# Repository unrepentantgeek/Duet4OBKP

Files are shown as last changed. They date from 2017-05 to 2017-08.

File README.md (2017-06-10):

# Duet4OBKP
Duet Wifi upgrades for the OpenBeam Kossel Pro

## Introduction
This is a set of 3D printed parts and instructions to upgrade the OpenBeam Kossel Pro to use the Duet Wifi (or Duet Ethernet) electronics.  The parts may also fit other printers that share similar geometry.

## The basics
The basic upgrade requires only the Duet motherboard and a 30mm fan, plus two printed parts for mounting and protecting the electronics.
  * Duet Wifi [US](https://www.filastruder.com/collections/electronics/products/duet-wifi) [EU](https://www.duet3d.com/DuetWifi)
  * 30mm 5V fan
  * [Panel mount USB cable](https://www.adafruit.com/product/937) (optional)

## Touchscreen
The PanelDue controller and touchscreen give you front panel monitoring and access to most of the functions of the printer.  It is available in 3 screen sizes, and printed enclosures are available for each.  Note that the 7" display enclosure is very large and may require removal of two bed clamps to be printable on the Kossel Pro.
  * PanelDue [US](https://www.filastruder.com/collections/electronics/products/paneldue) [EU](https://www.duet3d.com/DuetAddons/PanelDue)

## Hotend
The E3D hotend is one of the best, and the E3D lite is an amazing value.  With a couple of printed parts the end effector can be upgraded to fit either one.  Just make sure that you get the 24v heater to match the Kossel Pro's power supply.  You will also need to obtain another 5v 30mm fan (4.3CFM) as the Kossel Pro end effector PCB cannot handle 24v.
  * E3D Lite V6 (24v bowden) [US](https://www.filastruder.com/products/lite6?variant=1283850628) [EU](http://e3d-online.com/Lite6-1.75mm-Bowden-24v)
  * E3D V6 (24v bowden) [US](https://www.filastruder.com/products/all-metal-e3d-v6-hotend?variant=1236046392) [EU](http://e3d-online.com/E3D-v6/Full-Kit/175-universal-bowden-full-kit)
  * 30mm 5v fan (4.3CFM)

## Streaming webcam
You can mount a Raspberry Pi Zero W in the offical case with a camera and cheap wide angle lens to get streaming video in the web interface of your printer.
  * [Raspberry Pi Zero W Camera pack](https://www.adafruit.com/product/3414)
  * [Wide angle cell phone lens](https://www.amazon.com/Aduro-Universal-Magnetic-Detachable-Smartphones/dp/B01N2REG4L)

## PEI/Ultem print surface
This is an inexpensive and highly recommended upgrade for improved bed adhesion.
  * [Gizmo Dorks PEI Sheet](https://www.amazon.com/Gizmo-Dorks-Printing-Surface-Adhesive/dp/B01KGDTNQ2)

## The process
* [Preparation](Preparation.md)
* [Assembly](Assembly.md)
* [Configuration](Configuration.md)
* [Calibration](Calibration.md)

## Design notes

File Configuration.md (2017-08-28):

# Configuration

## Offline

Power down your printer and remove the micro-SD card from the Duet and connect it to your computer.  Copy the files in [sys](sys) to /sys on the SD card, overwriting files of the same name.

## Online

Follow the [directions to get your Duet online](https://duet3d.com/wiki/Getting_connected_to_the_Duet_WiFi) and use the web interface (settings tab) to update the contents of the corresponding files in [sys](sys).

### M500 and M501

* Note: Your Duet must be running ReprapFirmware 1.17 or higher for M500/M501 support.  [How to check your firmware version](https://duet3d.com/wiki/Checking_the_firmware_versions_and_updating_the_firmware)

The `M500` command will write out your system calibration to `/sys/config-overrides.g`.  Running the `M501` command will load that file and set those parameters.  To simplify recalibration we have added the `M501` command to the end of the `config.g` file.  Any time you want to save your current settings run `M500` and they will be stored for loading at the next reset.  The settings stored by `M500` are:

  * Delta parameters (`M666` and `M665`)
  * Heater paramters (`M307`)
  * Z probe parameters (`G31`)

The rest of the instructions assume that you will use `M500` to store these settings.

### Updating your configs

You can update config.g directly, or write overrides into local.g which is executed at the end of config.g, but before the calibration settings are loaded with `M501`.  If you use local.g then you can easily update config.g from this repository while maintaining your own changes.

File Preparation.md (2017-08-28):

## Tools
The tools that came with your Kossel Pro will get you most of the way.  You'll also need to buy or borrow some specialized tools for terminating the wires for the new connections:

- [Ferrule Crimper with Ferrules](https://www.amazon.com/gp/product/B01K160CC8/)
- [Ratcheting crimp pliers](https://www.adafruit.com/product/1213)
- [Wire stripper](https://www.amazon.com/IRWIN-VISE-GRIP-Self-Adjusting-Stripper-2078300)

A 2.5mm drill and an M3 tap are also recommended for forming threads in the plastic parts.

## Print the parts

## Strip the printer
Unplug power first and let it sit a few minutes at least.

To ease disassebly, you can cut the power input and heated bed output wires right at the Brainwave Pro motherboard.  We will
re-use these wires with new ends on them during assembly.

Disassembly:
  Remove end effector
  Remove delta arms
  Remove print glass & heated bed
  Remove bed clamp assemblies
  Remove power inlet/switch bulkhead and wires to the PSU
  Disconnect all wires and remove Brainwave Pro mainboard
  Remove extruder cold end assembly

If you didn't add the extra m3 nuts to the lower frame rails as recommended in the assembly guide, then you'll need to go back now and add them.  This is an exercise left to the reader, but turning the printer upside down and removing one rail at a time can be helpful.

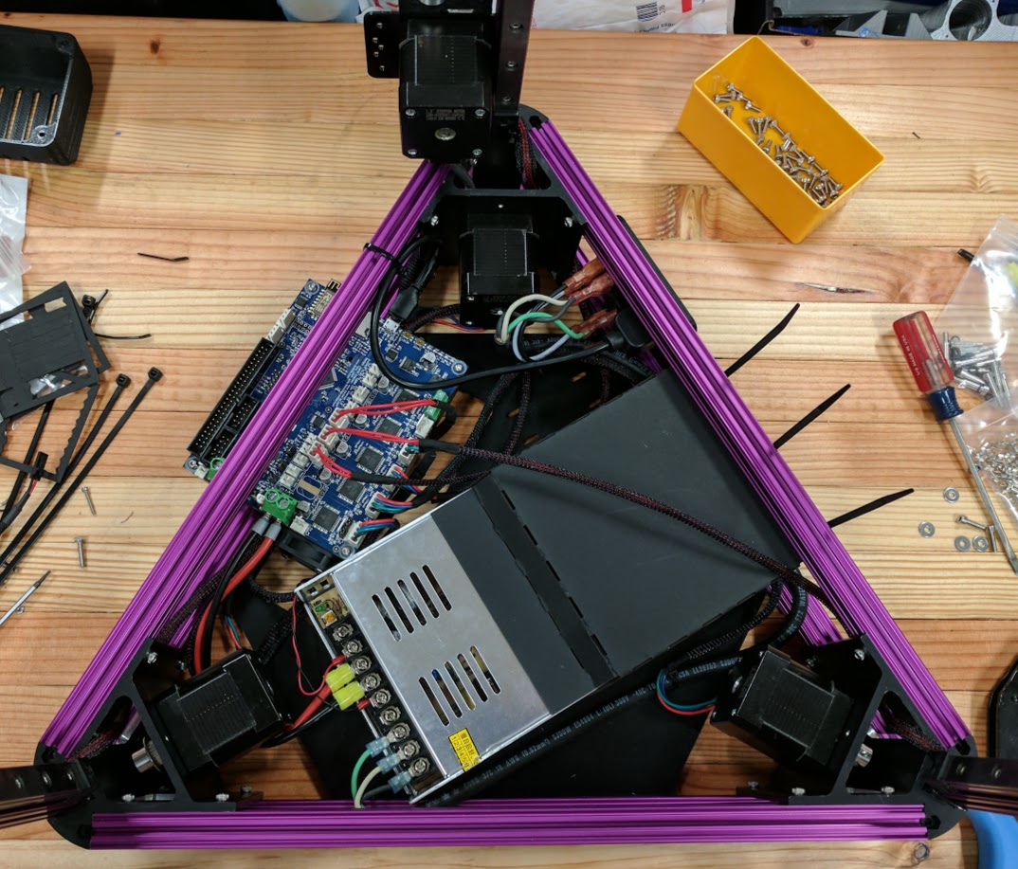
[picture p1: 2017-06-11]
img/lower_frame.jpg

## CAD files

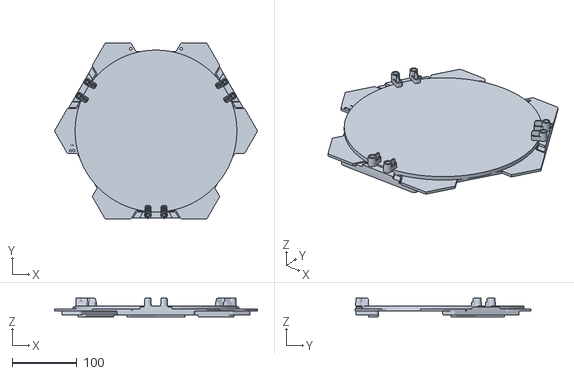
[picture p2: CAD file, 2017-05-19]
slicer_configs/openbeamkosselpro.stl
313.8 x 272.0 x 29.0

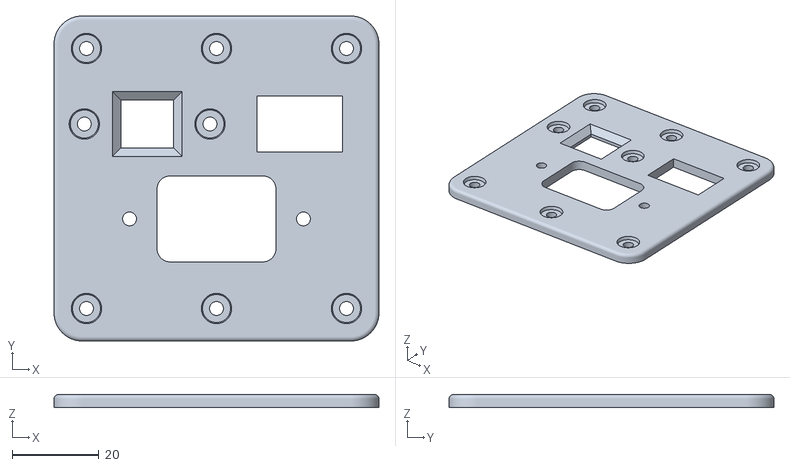
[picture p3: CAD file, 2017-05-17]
stl/Combination Bulkhead.stl
75.0 x 75.0 x 3.00

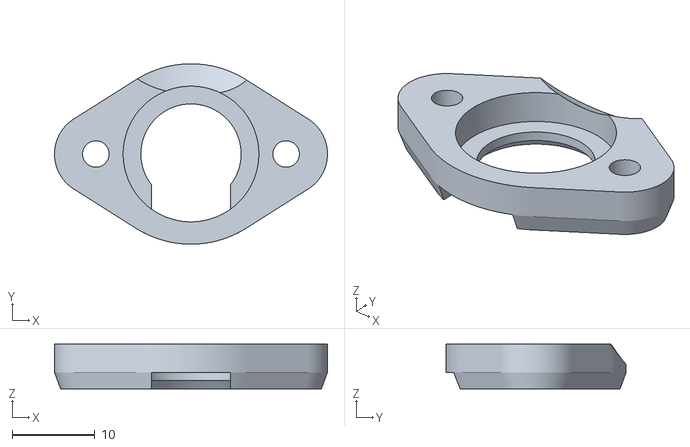
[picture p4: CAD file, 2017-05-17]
stl/Hot end clamp - Upper.stl
33.0 x 21.8 x 5.40

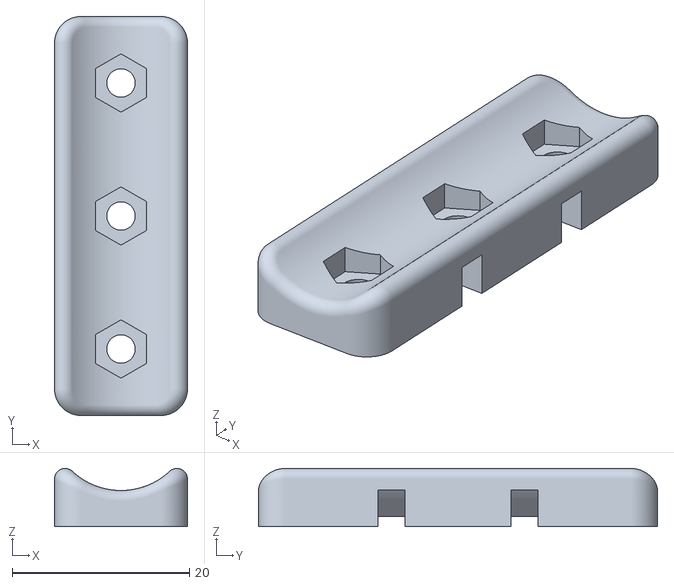
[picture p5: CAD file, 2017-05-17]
stl/Wire Mount.stl
15.0 x 45.0 x 6.56

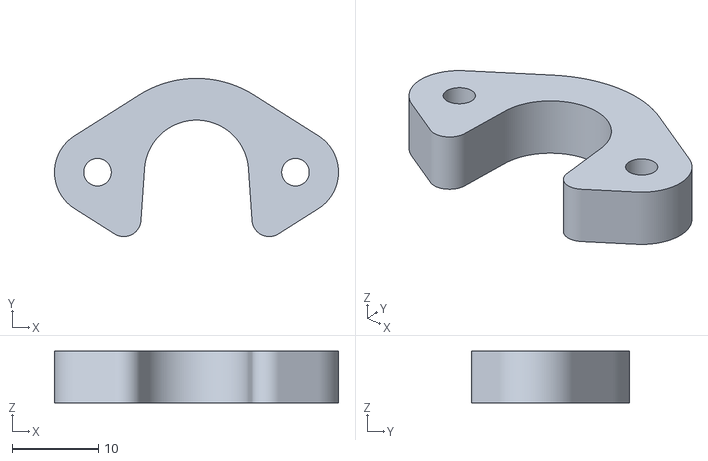
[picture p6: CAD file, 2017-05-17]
stl/Hot end clamp - Lower.stl
33.0 x 18.4 x 6.00

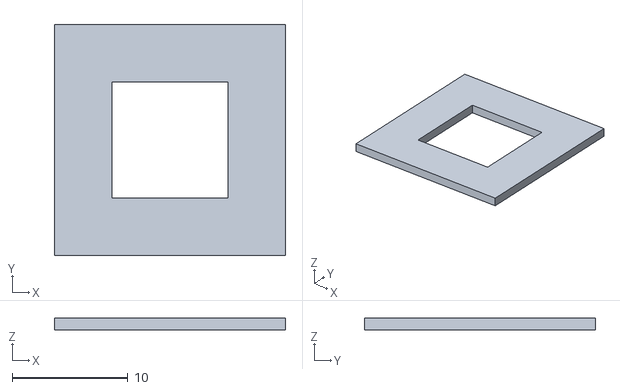
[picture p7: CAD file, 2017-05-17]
stl/Calibration Square.stl
20.0 x 20.0 x 1.00

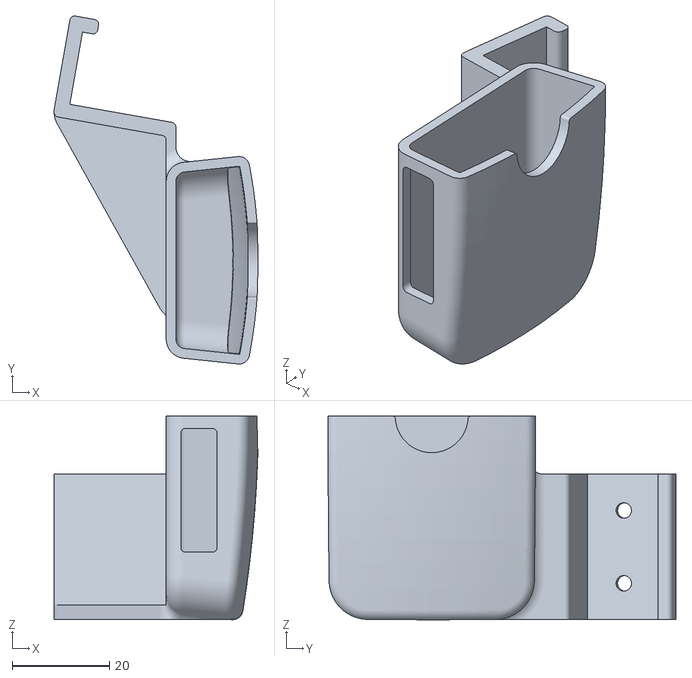
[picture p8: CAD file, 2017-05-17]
stl/Pi Zero Camera Mount.stl
42.0 x 71.7 x 41.9

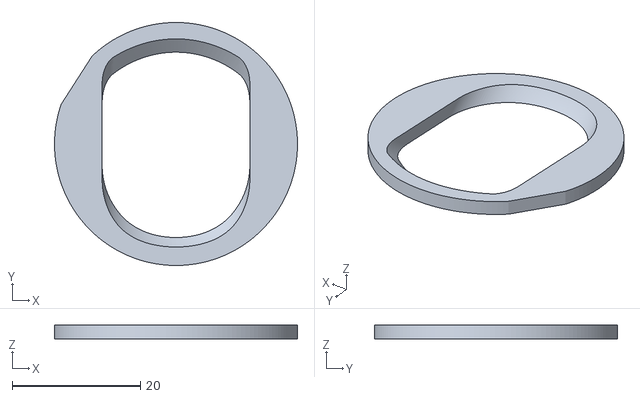
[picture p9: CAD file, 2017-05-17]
stl/End Effector Baffle.stl
37.8 x 37.8 x 2.20

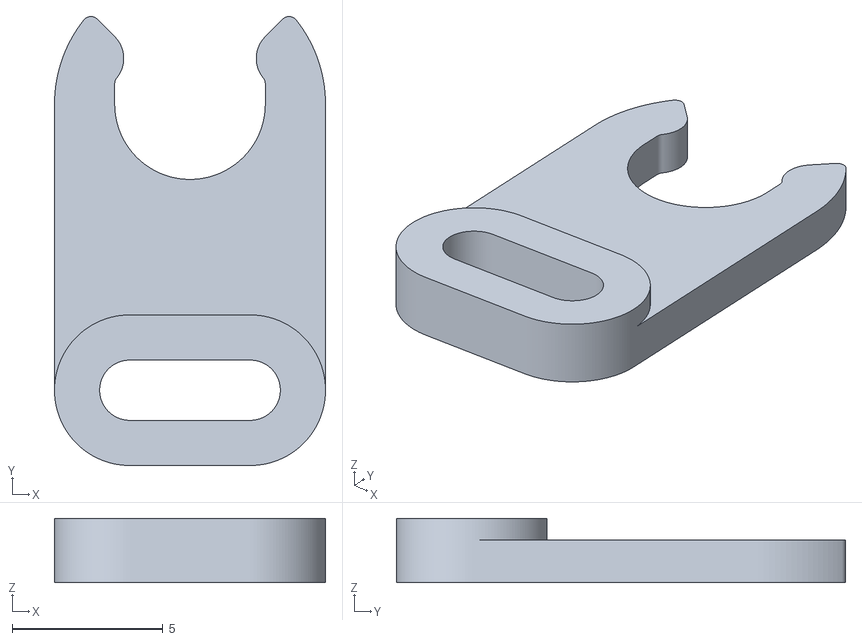
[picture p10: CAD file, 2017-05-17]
stl/Bowden Locking Tab.stl
9.00 x 14.9 x 2.14

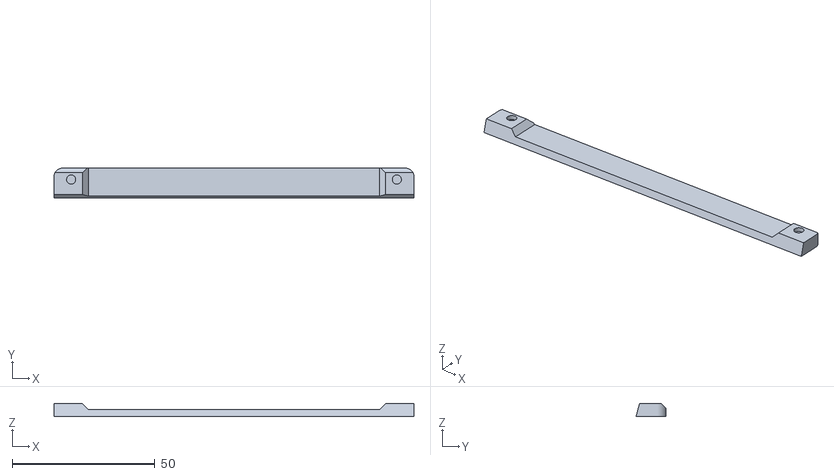
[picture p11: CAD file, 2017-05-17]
stl/PanelDue Enclosure 4.3 Nut Bracket.stl
126.0 x 10.4 x 4.40

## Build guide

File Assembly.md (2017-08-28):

# Assembly

## Install Duet

**VERY IMPORTANT: Move the VFAN jumper to the 5v position.  24V will fry the LEDs in the end effector PCB!**

Tap the two holes around the fan mounting location with an M3 tap.  Install a 30mm fan using ???mm M3 bolts.  If this is a 24v fan, you will wire it to the PSU directly.  If it's a 5v fan, you can wire it to one of the always-on fan headers on the mainboard.

Install the Duet board onto it's mounting bracket with some M3 bolts and nuts.  Be sure to use the plastic washers included with the Duet to prevent shorting out the board.  You can now mount this assembly into the frame using two M3 x 6 bolts into the side of the lower rail between the X and Z towers.  Make sure to leave at least one nut in the rail on either side of this bracket to allow you to mount the cover later.

### Wiring

While you can just plug the wires into the Duet it is recommened that you cut off the old connectors and crimp on the connectors included with the Duet.

You must re-terminate one end of the end effector umbilical.  The connections on the Duet are sufficiently different that you can't just plug in.  See the image below for the correct pin connections.
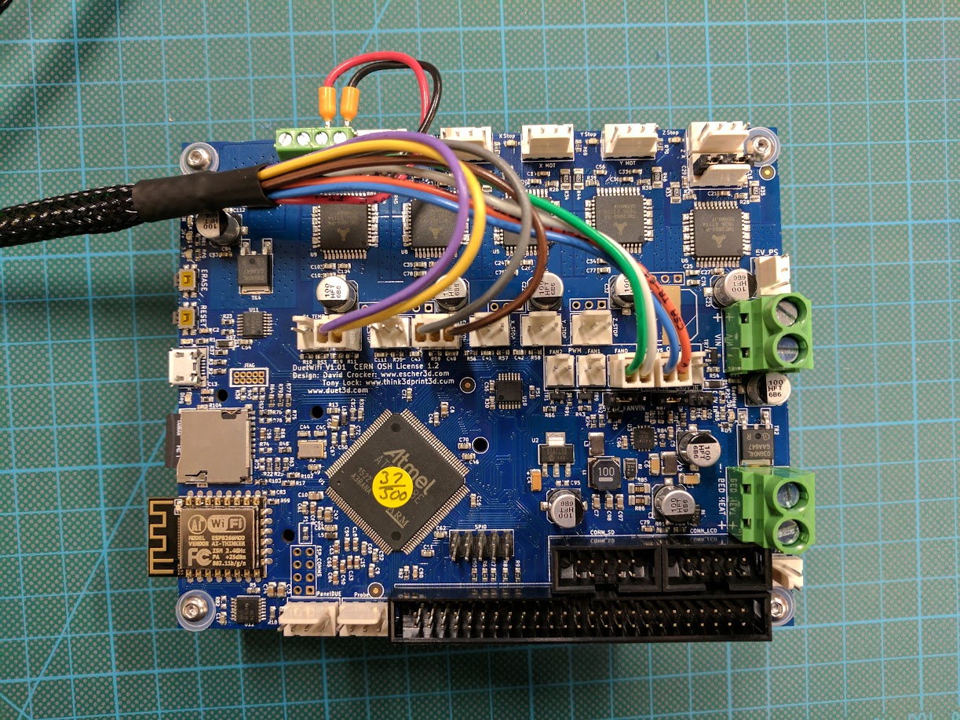
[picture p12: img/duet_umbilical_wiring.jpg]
Umbilical wiring


## Power bulkhead
If you are going to install the USB extension cable then migrate the power inlet and switch to the new power bulkhead.  The remaining holes are for the USB extension.  Install it with two M3 screws or bolts.

The newly assembled bulkhead is installed on the lower rails between the Z vertex and the PSU air outlet.  This is different from the original layout.
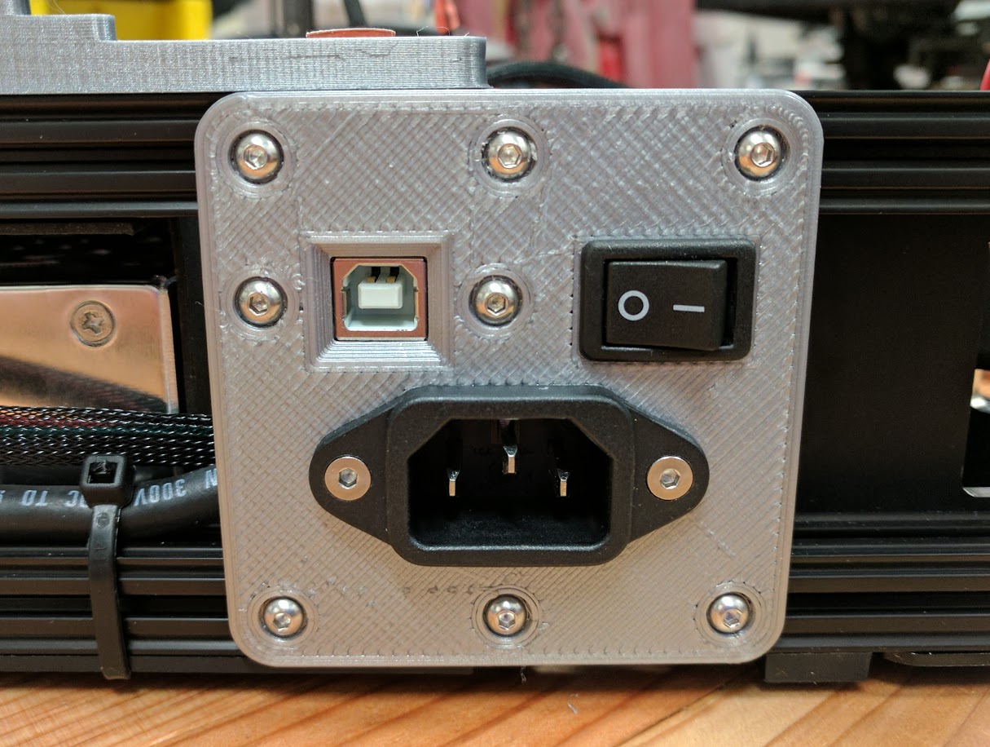
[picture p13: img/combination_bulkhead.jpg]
combination bulkhead


## End effector

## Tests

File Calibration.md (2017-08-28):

# Calibration

## Calibrate PID

The thermistor is configured with the `M305` command.  Make sure to use the right value for B and C for your setup.  For the E3D v6 and v6 lite, the correct setting for extruder 0 is `M305 P1 T100000 B4725 R4700 C7.06e-8 H30 L0`

To start a PID tune, run the following command on the gcode console:

```M303 H1 S220 P1```

**Don't walk away!**  Keep an eye on the temperature until the heater has turned off.  If the firmware reports that the heater is overpowered, then wait for the heater to cool and re-run the `M303` command above with a lower value for P i.e.: `M303 H1 S220 P0.5`

Save the PID tuning values with `M500`

For more information on heater control and tuning see https://duet3d.com/wiki/Tuning_the_heater_temperature_control

## Calibrate Z probe

Home all axes and then drive the end effector down to just touch the bed.  If you hit Z=0 before you reach the bed use `G92 Z10` to reset the Z axis and continue to move down with the jog controls.  Use a piece of paper to ensure that you are *just* touching the bed.  The paper should drag under the nozzle, but not be pinned down to the bed.

Once you are just touching the bed run `G92 Z0` to zero the Z axis.  Then move up 20mm, manually deploy the Z probe and run `G30 S-1`.  The end effector will move down slowly until the probe triggers.  Your probe offset will be printed to the gcode console.  It is recommended that you repeat this process several times until the value settles down.

Update the probe offset with the G31 command.  For example `G31 Z12.345`  Then run `M500` to store the config.

## Auto level

Deploy the Z-probe and run the Auto Delta Calibration command `G32` or press the button in the interface.  You may want to run this a couple of times until the reported deviation settles down.  If the printer reports untriggered probe points then increase the `H` parameter of the `M665` command in config-override.g by 5 at a time until all probe points trigger.

Run the `M665` and `M666` commands and inspect the output:

```
M665
Diagonal 300.000, delta radius 152.665, homed height 272.993, bed radius 135.0, X -0.231°, Y -0.860°, Z 0.000°
M666
Endstop adjustments X-0.35 Y-0.95 Z1.30, tilt X0.00% Y0.00%
```

These are the computed values for your delta geometry.  Save them by issuing an `M500` command.  You might also want to copy these values to local.g so that you have a sane base config to go back to should you incorrectly overwrite config-overrides.g.

## Adjusting for varying probe offset

The probe offset likely changes slightly depending on where across the bed the printer is probing.  This can be caused by a number of factors, but it's relatively easy to compensate for.  Open `bed.g` and note the locations that your printer probes at.  At the end of each G30 command is an H0 operand.  That's the probe offset for that location.

First, home your printer and then use the `M561` command to cancel any existing bed compensation.  Next, jog the head to each location listed in `bed.g` and measure it according to the instructions below.  You can do this quickly with the `G01` command:

```G01 X45.47 Y26.25 Z1```

The above example command moves the nozzle to 1mm above the bed at the specified X,Y coordinates.  Carefully jog down 0.05mm at a time until a piece of paper just drags under the nozzle, just like when calibrating the z-probe.  Note the Z value of where this happens.  **Invert** this probe offset value and use it for the H value of this G30 line in `bed.g`.  Repeat for all locations and update/save your `bed.g` file.  For example:

```
; If you measure a Z value of 0.05 for this line:
G30 P1  X45.47 Y26.25 Z-99999 H0
; It should be updated to look something like this:
G30 P1  X45.47 Y26.25 Z-99999 H-0.05
```

Note: when moving from one X/Y location to another, it's a good idea to move up at least 1mm to avoid dragging the nozzle!

Hint: By default the web interface has buttons for .1mm moves but you can change this to 0.05mm by checking the 'Half Z Movements' checkbox under the 'User Interface' tab in the system settings.  If you'd like even more fine grained control you can create your own macros for "Move Up 0.01mm" and "Move Down 0.01mm" by using the following example gcode:

```
G91             ; change to relative moves
G1 Z0.01 F2000  ; or Z-0.01 to move down
G90             ; restore absolute moves
```

# First print

Print the [Calibration Square.stl](stl/Calibration%20Square.stl).  If you have set any slicer tweaks such as 'Inset surface' or 'Horizontal size compensation' you should disable them for now.  Once the print is complete, mark the front top with a marker for reference, and remove it from the print bed.

Measure the thickness at several points around the perimiter.  It should be 5mm thick.  Otherwise:

  * Consistently thin or thick
  
  Your probe offset is incorrect.  If the part is too thin, *reduce* the probe offset by how much thinner than 5mm the part is.  Then repeat the bed probe and save the values.
  
  * Inconsistent thickness
  
    * Doublecheck that you got the sign right on the H values when fine tuning probe offset
    * Make sure that your printer doesn't have any loose screws

## Compensate for too thin/thick a first layer

When you start your first print, watch how the first layer is sticking.  You can use the baby step buttons on the web or LCD interface to nudge the nozzle up and down by 0.5mm.  If you find that you need to adjust for the first layer, note the value of the baby step.  Go into config-overrides.g and **subtract** that value from the Z Probe offset (G31 command).

For example if your printer requires to be baby stepped up by 0.15mm and your G31 Z value is 12.80, change the Z value to 12.65.

Save the config-override.g file, reset the printer and re-run the bed levelling command.  Try a print to test your new setting.  If it's good, run `M500` to save your new bed level.

## Compensate for X/Y shrinkage

Use `M579` to compensate for any growth or shrinkage in X and Y caused by innacuracies in the delta geometry.  For example if your printer consistently prints parts 1% too small, use: `G579 X1.01 Y1.01`

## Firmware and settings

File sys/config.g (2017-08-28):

; Think3DPrint3D configuration file for Mini Kossel for testing Duet WiFi

; Communication and general
M111 S0                             	; Debug off

M555 P2                           	; Set output to look like Marlin
M575 P1 B57600 S1			; Comms parameters for PanelDue

G21                                 	; Work in millimetres
G90                                	; Send absolute coordinates...
M83                                 	; ...but relative extruder moves

; Axis and motor configuration
M569 P0 S0				; Drive 0 goes backwards
M569 P1 S0				; Drive 1 goes backwards
M569 P2 S0				; Drive 2 goes backwards
M569 P3 S1				; Drive 3 goes forwards
M569 P4 S1				; Drive 4 goes forwards
M574 X2 Y2 Z2 S1			; set endstop configuration (all endstops at high end, active high)
;*** The homed height (H270) is deliberately set too high in the following line.
;*** You will adjust it during calibration (higher number is closer to the bed).
M665 L300.000 R153 H270 B135.0 X0 Y0 Z0	; set delta radius, diagonal rod length, printable radius and homed height
M666 X0 Y0 Z0 A0.00 B0.00		; put your endstop adjustments here, or let auto calibration find them
M350 X16 Y16 E16 I1    			; Set 16x microstepping with interpolation
M92 X80 Y80 Z80				; Set axis steps/mm
M906 X1000 Y1000 Z1000 E800 I60		; Set motor currents (mA) and increase idle current to 60%
M201 X1000 Y1000 Z1000 E1000		; Accelerations (mm/s^2)
M203 X20000 Y20000 Z20000 E3600		; Maximum speeds (mm/min)
M566 X1200 Y1200 Z1200 E1200		; Maximum instant speed changes mm/minute

; Thermistors
M305 P0 T100000 B3950 R4700 H30 L0	; Put your own H and/or L values here to set the bed thermistor ADC correction
M305 P1 T100000 B4725 R4700 C7.06e-8 H30 L0	; Put your own H and/or L values here to set the first nozzle thermistor ADC correction
M305 P2 T100000 B3974 R4700 H30 L0	; Put your own H and/or L values here to set the second nozzle thermistor ADC correction
;M570 S180				; Hot end may be a little slow to heat up so allow it 180 seconds

; PID - Run calibration, uncomment this and put your vaules here
;M307 H1 A377.3 C149.2 D4.5 S1.00 B0

; Fans
M106 P1 H-1 				; disable thermostatic mode for fan 1

; Tool definitions
M563 P0 D0 H1                       	; Define tool 0
G10 P0 S0 R0                        	; Set tool 0 operating and standby temperatures
;*** If you have a single-nozzle build, comment the next 2 lines
;M563 P1 D1 H2                      	; Define tool 1
;G10 P1 S0 R0                       	; Set tool 1 operating and standby temperatures
M92 E92.6:92.6                       	; Set extruder steps per mm

; Z probe and compensation definition
;*** If you have a switch instead of an IR probe, change P1 to P4 in the following M558 command
M558 P4 X0 Y0 Z0			; Z probe is a mechanical probe and is not used for homing any axes
; Update Z value based on M30 probe report
G31 X0 Y0 Z11.959 P500			; Set the zprobe height and threshold (put your own values here)

;*** If you are using axis compensation, put the figures in the following command
M556 S78 X0 Y0 Z0                   	; Axis compensation here

M208 S1 Z-0.2				; set minimum Z
;
T0					; select first hot end

M98 Plocal.g ; Load local settings

; load values from config-overrides.g at boot
M501

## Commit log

2017-05-01 calibration object
    [calibration-frame.stl]
2017-05-17 Add printed parts
    [Bowden Locking Tab.stl, Calibration Square.stl, Combination Bulkhead.stl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]
2017-05-17 orient parts for printing
    [Combination Bulkhead.stl, Hot end clamp - Upper.stl, PanelDue Enclosure 4.3 Nut Bracket.stl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]
2017-05-19 simplify3d configs and bed stl file
    [openbeamkosselpro.stl]
2017-05-21 Update calibration.md
    fix some typos, clarify a bit
2017-05-21 base configs
    [bed.g, config.g, homedelta.g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]
2017-06-03 Files for retract/deploy probe: e3d version
    [deployprobe.g, retractprobe.g]
2017-06-03 Rewrite varying-probe-offset for clarity
    Most importantly, adjust default values so user doesn't cause a
    head crash if it's just pasted into the control interface before
    reading what's actually supposed to happen.
2017-06-03 home before running bed probe
    User probably should have done this already, but better things just work
    instead of them seeing an error message.
    [bed.g]
2017-06-03 Add commented-out lines for probe deploy/retract
    [bed.g]
2017-06-03 Reword comments for clarity
    [config.g]
2017-06-03 Fix link to Calibration Square.stl
2017-06-04 rethink default wifi config
    [config.g]
2017-06-10 add image of umbilical wiring
2017-07-10 Update config.g
    260 is too low (probe doesn't trigger)
    [config.g]
